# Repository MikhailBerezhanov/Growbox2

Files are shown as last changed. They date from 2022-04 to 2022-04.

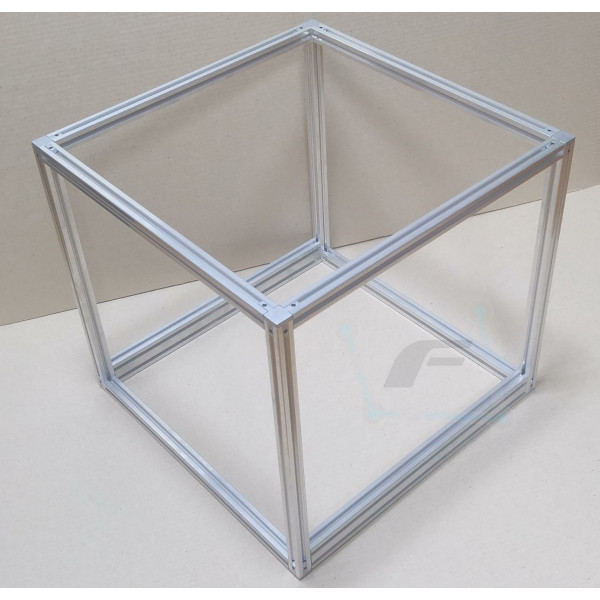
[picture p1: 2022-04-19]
case_design/3D_body/Чертежи/DY-4044-1-600x600.jpg

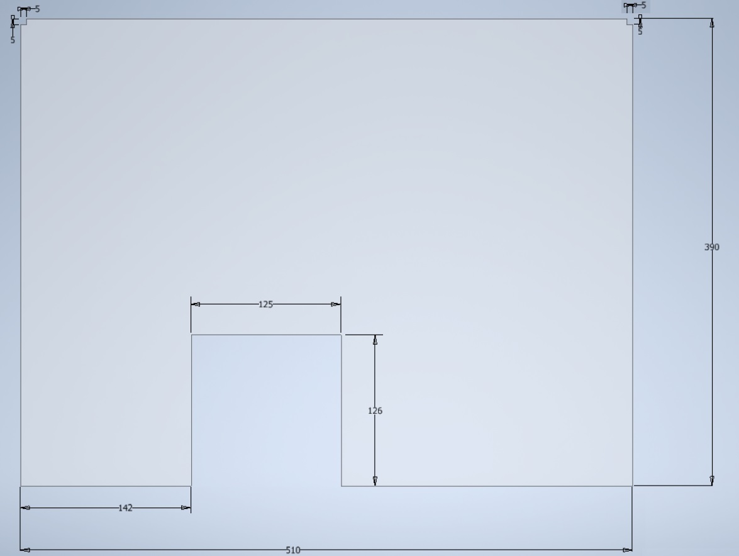
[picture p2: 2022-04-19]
case_design/3D_body/Чертежи/БокСтенка1.jpg

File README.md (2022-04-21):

# Growbox2
### Automated plants growing indoor system

([Learn more about this project](https://habr.com/ru/post/521414/))

3Dmodel

Growbox2 is an indoor system that takes care of your plants. It helps with:

* Watering
* Lighting
* Climate control

It supports WEB-UI to configure and check all function.



### How does it work

The system is based on 3 boards: 

* __Khadas VIM1__ - host MPU
* __FLC-01__ - self-made fitolamp controller
* __SensorsController__ - some kind of adapter from sensors-data to I2C bus 

Connection is the following:  



Host board runs __Ubuntu18.04 Linux__ and provides WEB-server that is available via Ethernet or WIFI connection.  
WEB interface is based on AJAX technology, so any sensor data is updated by request. You can use your __Browser__ to configure and watch the box system parameters. 

### IP address settings

There are different options in Growbox IP address configuration:

* __WIFI connection__ - by default system runs in WIFI Access Point (AP) mode, so using your smartphone you can
  1. find wifi-net called _Growbox_, 
  2. connect it, 
  3. see UI from mobile browser.  
That allows you to perform further configuration. 

*Technically WIFI mode could be configured to Client mode for wireless connection with your router, but this feature not implemented yet in _Settings_ menu.

* __LAN connection__ - by default system has dynamic IP (DHCP is on), so you'll need to
  1. check what address device got in your router menu,
  2. open this IP in Browser to get access to system UI   
Afterwards, LAN IP address can be changed to static in _Settings_ menu.

### Software

UI backend part is the CGI-application that runs on NGINX webserver.  

For _Debian \ Ubuntu_ backend dependencies installed as:  
`sudo apt install gcc g++ make nginx sqlite3 libconfig-dev libfcgi-dev libsqlite3-dev isc-dhcp-server hostapd`

Frontend part can be found in `UI/data` subfolder and has all dependencies inside to let system work without Internet connection.

Optionally application can be installed on target by calling `UI/install.sh` script. That will add __systemd__ service that can be controlled by _systemctl_ commands:

``` sh
# Run backend and check it's status
systemctl start gbweb
systemctl status gbweb
# Stop backend
systemctl stop gbweb
```

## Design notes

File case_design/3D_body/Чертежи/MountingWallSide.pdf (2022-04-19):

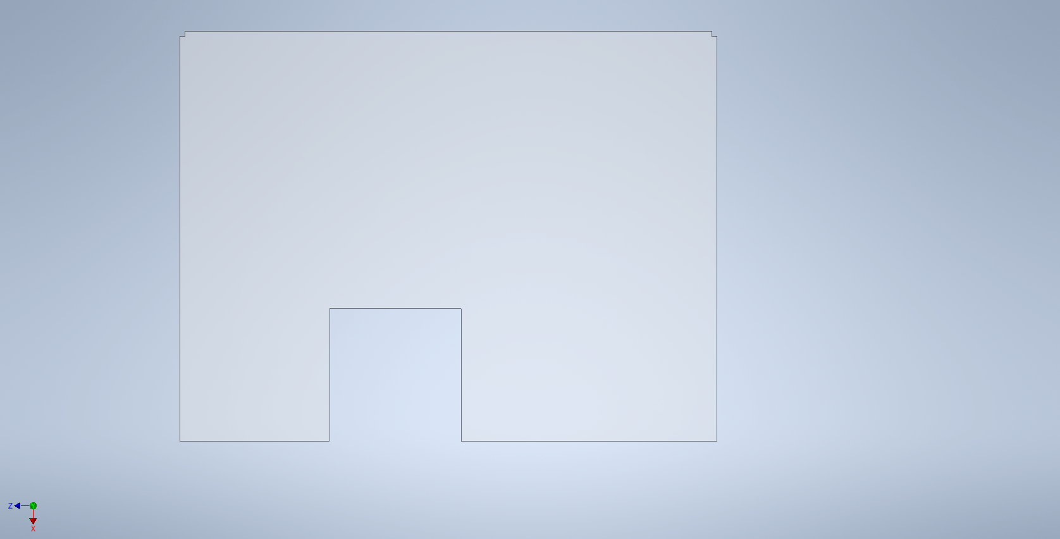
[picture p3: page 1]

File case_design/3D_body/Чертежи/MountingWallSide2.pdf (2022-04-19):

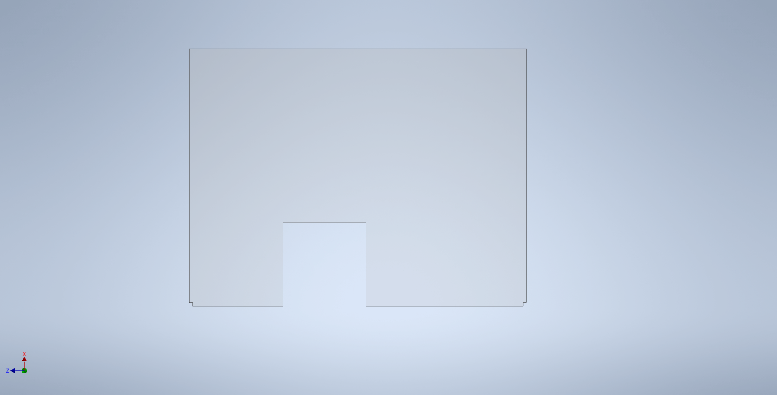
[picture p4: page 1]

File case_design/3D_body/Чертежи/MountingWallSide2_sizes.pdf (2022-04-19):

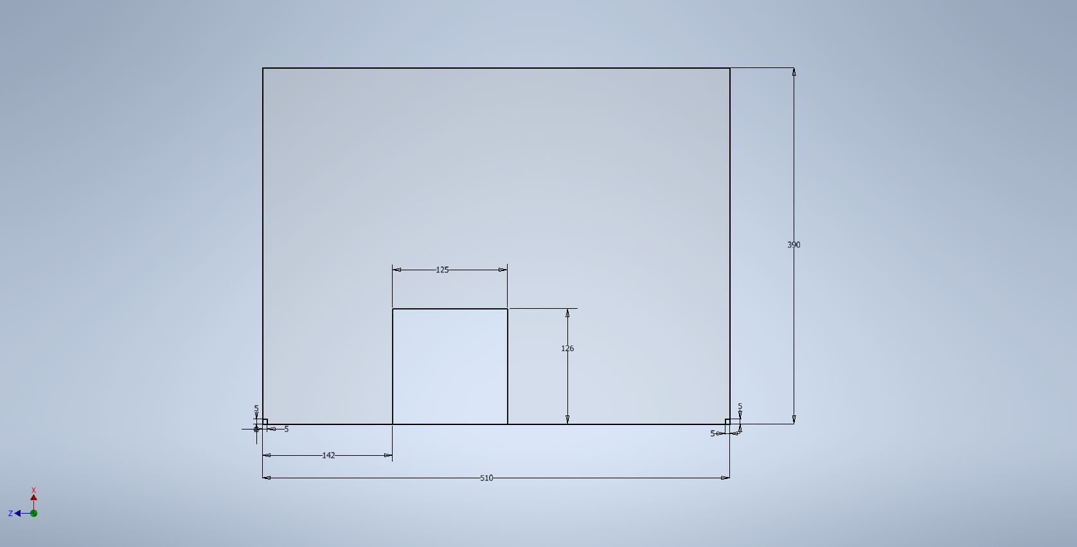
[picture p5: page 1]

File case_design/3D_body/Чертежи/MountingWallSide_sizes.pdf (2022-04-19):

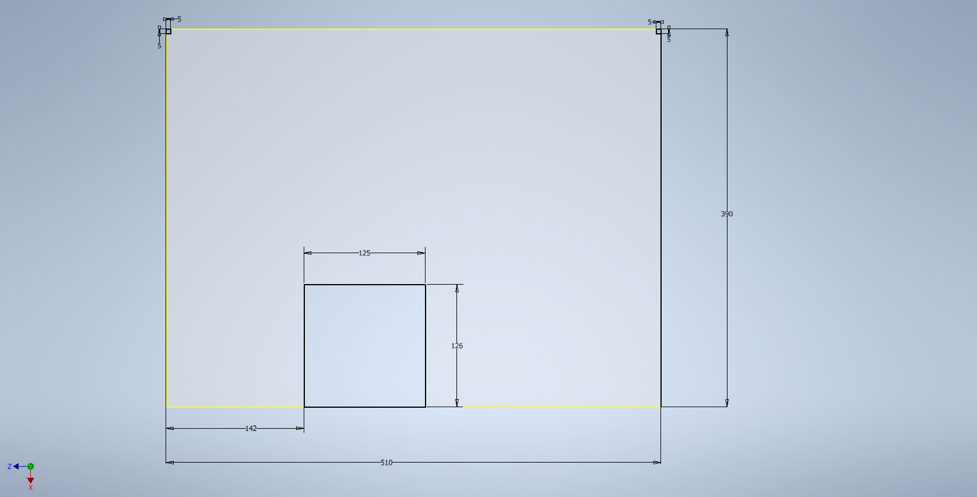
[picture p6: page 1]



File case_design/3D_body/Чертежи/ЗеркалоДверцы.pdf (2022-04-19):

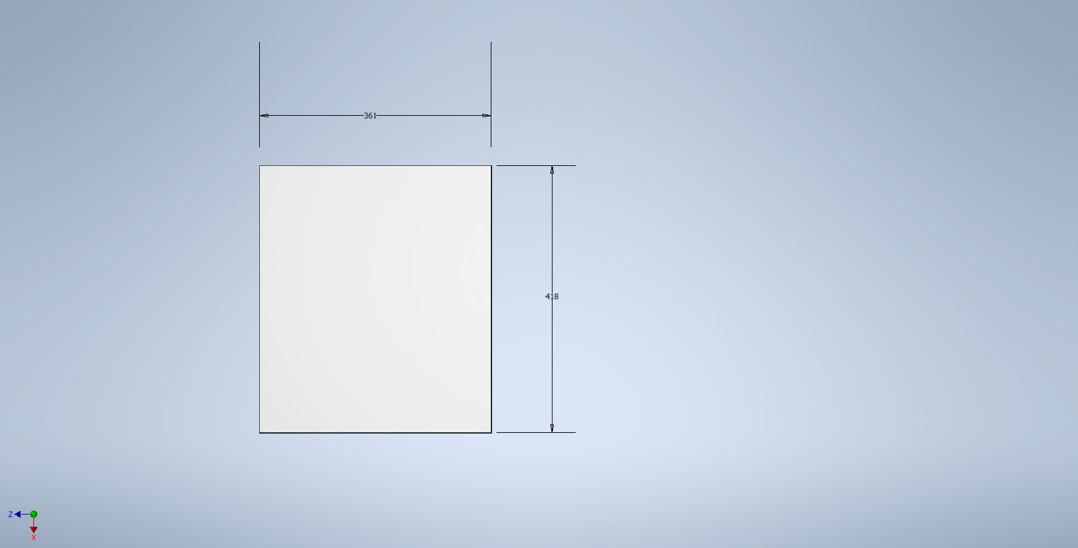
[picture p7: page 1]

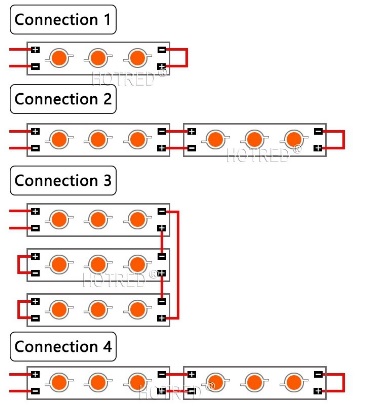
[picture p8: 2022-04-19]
case_design/led_strips_conn2.jpg

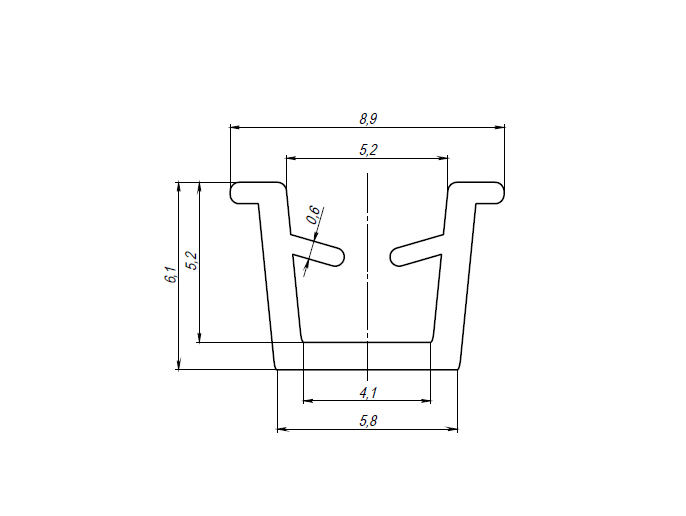
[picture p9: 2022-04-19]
case_design/Z19_chertezh.jpg

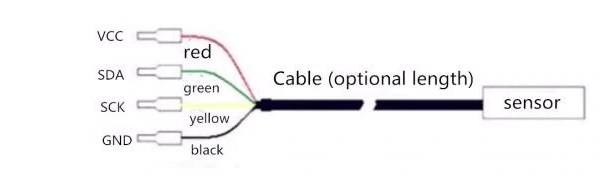
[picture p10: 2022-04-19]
boards/sensors/TempHumSensor/sensor_pinout.jpg

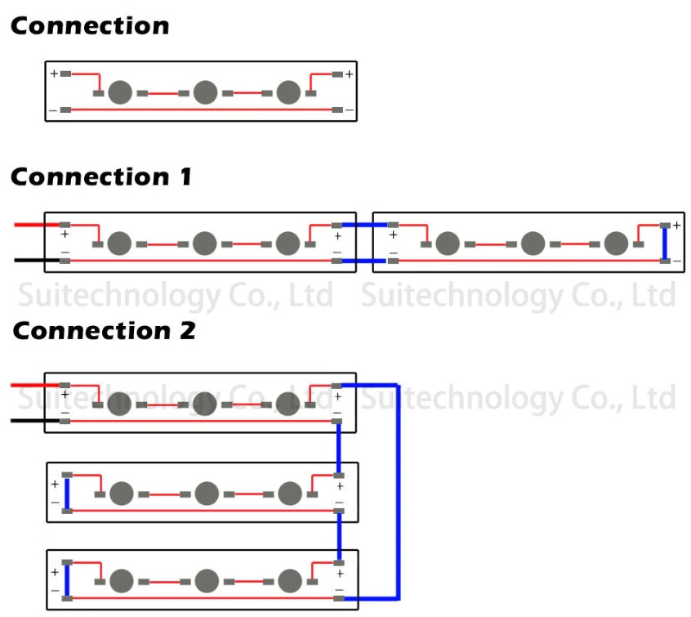
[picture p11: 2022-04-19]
case_design/led_strips_connection.jpg

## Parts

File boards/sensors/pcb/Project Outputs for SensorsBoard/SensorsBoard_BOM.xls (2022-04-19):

Comment | Description | Designator | Quantity
K50-35 63V 47uF | Конденсатор электролитический алюминиевый | C1 | 1
1210 1uF X7R 100V | Cap SMD1210 | C2 | 1
K50-35 35V 220uF | Конденсатор электролитический алюминиевый | C3 | 1
0805 1uF 25V X7R | SMD Cap 0805 | C4 | 1
K50-35 10V 100uF | Конденсатор электролитический алюминиевый | C5 | 1 | https://www.chipdip.ru/product0/311944248?from=suggest_product
LM2596HV - 12V | SIMPLE SWITCHER4; 4V to 60V, 3A Low Component Count Step-Down Regulator | DA1 | 1 | https://www.chipdip.ru/product/lm2596hvgr-12
КР142ЕН5А | Cтабилизатор напряжения положительной полярности с выходным напряжением 5 В | DA2 | 1 | https://www.chipdip.ru/product/kr142en5a
RDC1-0014 | Встраиваемый DC/DC преобразователь 60В 3А | DA3 | 1
STM32F103_BLUEPILL | STM32F103_BLUEPILL | DD1 | 1
RLB0914-470KL | Радиальные выводные индуктивности | L1 | 1
SRR1208-330YL | Fixed Inductors 6800uH 10% SMD 1208 | L2 | 1
0805 10k | SMD Res 0805 | R1, R2 | 2
7.5k 1% | Throu hole resistor | R3 | 1 | https://www.chipdip.ru/product0/43763
0805 0 | SMD Res 0805 | R4 | 1
BZX55C3V3 | Stabilitron 3.3V | VD1 | 1
SS36 | Rectifier, Schottky; DO-214AB; 3.0A IF; 0.75V; 60V; 100A IFRM; 10000V/us; 1000pF | VD2 | 1
SS26T3G | Диод Шоттки 2А 60В [SMB / DO-214AA] | VD3 | 1
DS1069-4M | Вилка на плату 2.50мм | X1 | 1
300-041-12 | Клеммник винтовой, 4-контактный, 5мм, прямой | X2 | 1
Conn_Molex_47053-1000_eec | CONN 4 Positions Header, Unshrouded Connector 0.100" (2.54mm) Through Hole Tin | X3 | 1
DS1021_1x4 | Вилка штыревая 2.54мм 1x4 прямая тип1 | X4, X5 | 2
Conn_Molex_47053-1000_eec | CONN 4 Positions Header, Unshrouded Connector 0.100" (2.54mm) Through Hole Tin | X6 | 1
DS1021_1x8 | Вилка штыревая 2.54мм 1x8 прямая тип1 | X7, X8 | 2
300-021-12 | Klemmnik 2 | X9 | 1

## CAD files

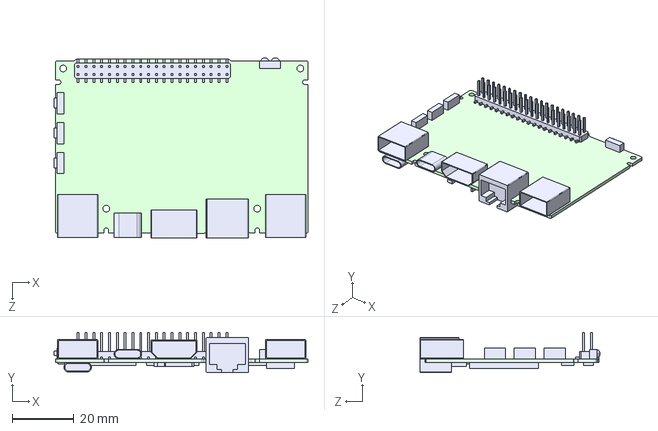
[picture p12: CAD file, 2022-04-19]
boards/host/Khadas VIM1/edge-v-11.STEP
82.5 x 13.1 x 58.6 mm

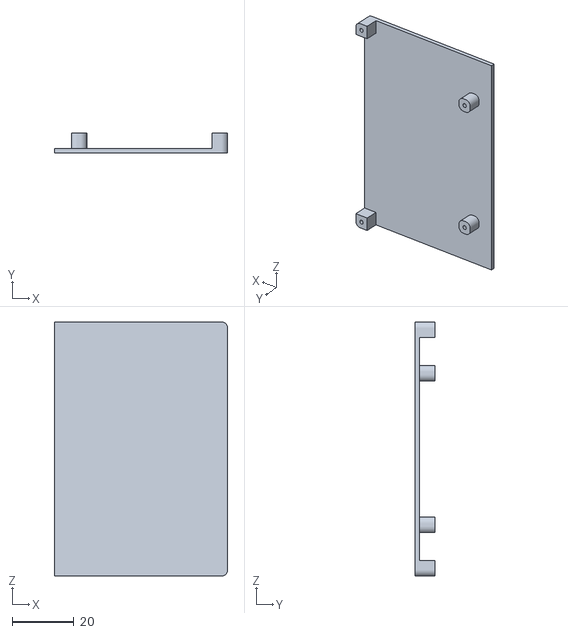
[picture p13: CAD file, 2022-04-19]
case_design/3D_body/ForPrint/VIM1_Holder.stl
56.0 x 6.50 x 82.0

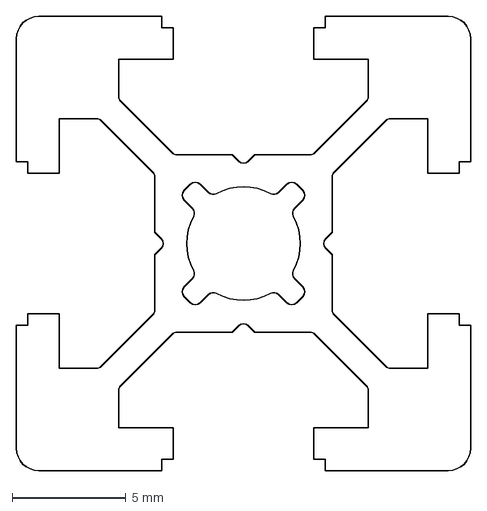
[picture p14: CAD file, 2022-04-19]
case_design/3D_body/Чертежи/OB-2020.DXF
20.0 x 20.0 mm

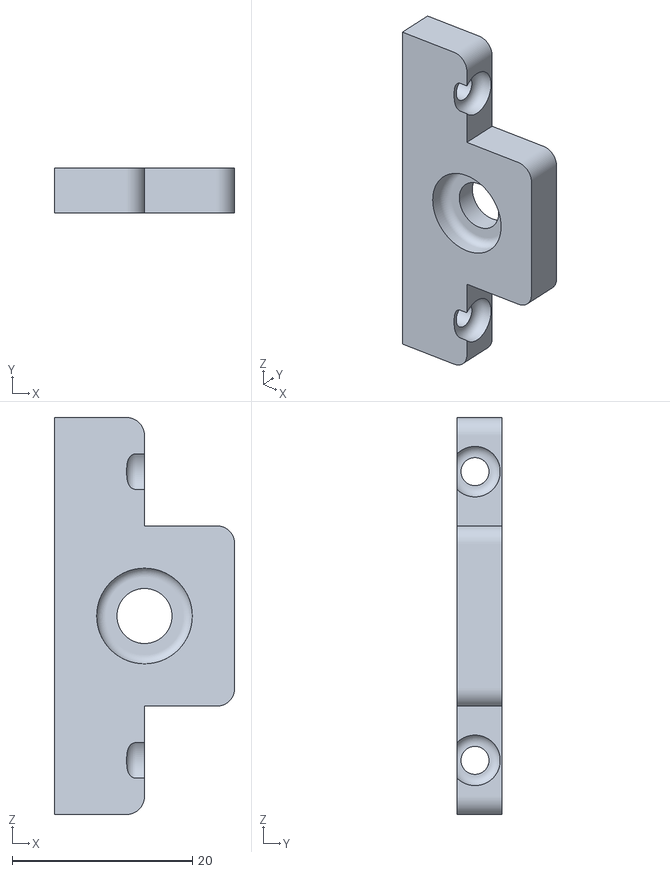
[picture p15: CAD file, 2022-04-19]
case_design/3D_body/ForPrint/RaditorFastener2.stl
20.0 x 5.00 x 44.0

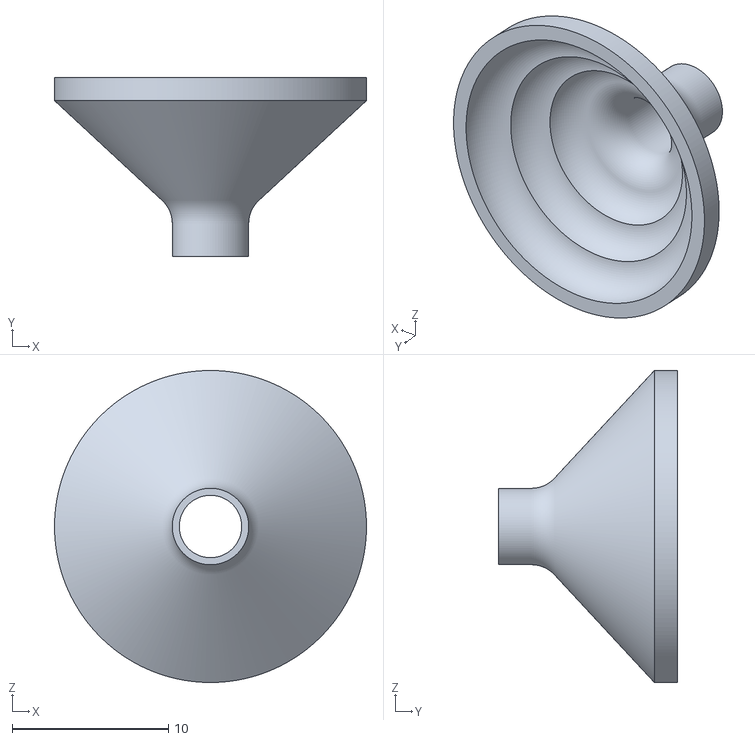
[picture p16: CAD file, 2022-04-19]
case_design/3D_body/ForPrint/TubeExpander.stl
20.0 x 11.5 x 20.0

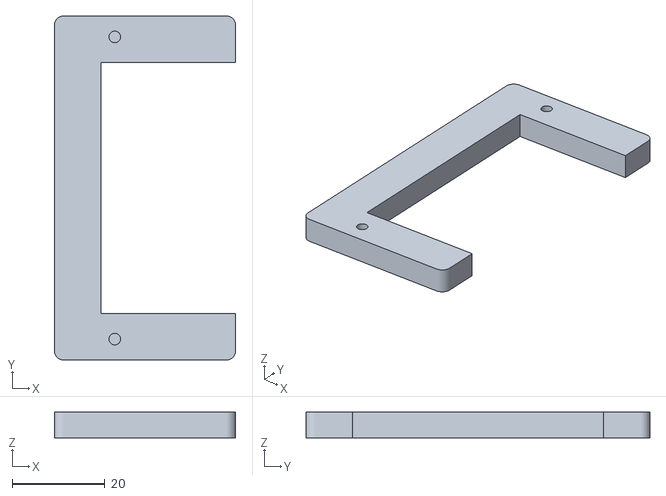
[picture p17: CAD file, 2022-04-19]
case_design/3D_body/ForPrint/S-10-5_Holder.stl
39.0 x 74.0 x 5.50

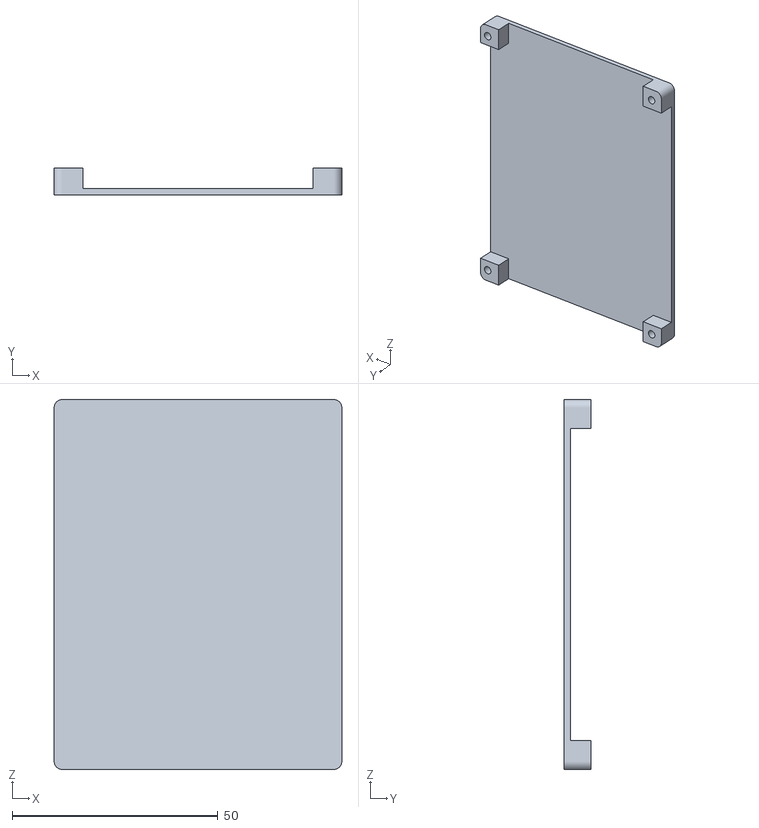
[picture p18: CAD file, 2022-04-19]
case_design/3D_body/ForPrint/SensorsC_Holder.stl
70.0 x 6.50 x 90.0

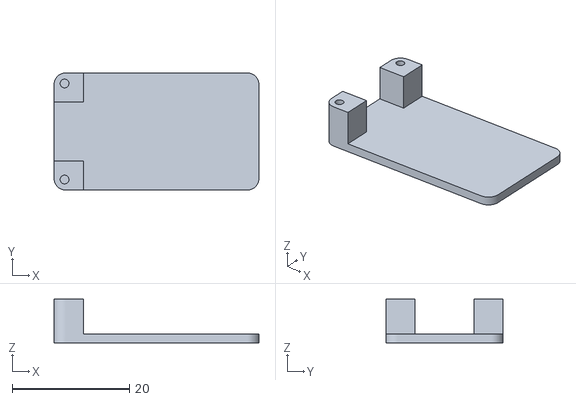
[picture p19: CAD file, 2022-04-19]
case_design/3D_body/ForPrint/RDC1-0014_Holder.stl
35.0 x 20.0 x 7.50

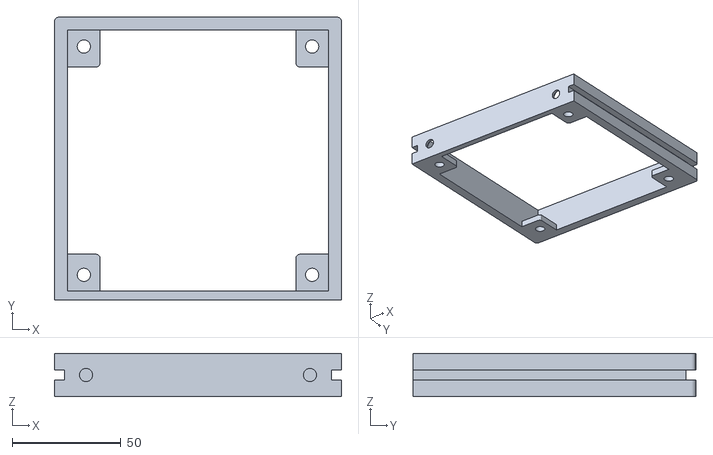
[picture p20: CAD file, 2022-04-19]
case_design/3D_body/ForPrint/CoolerFastener.stl
132.0 x 130.0 x 20.0

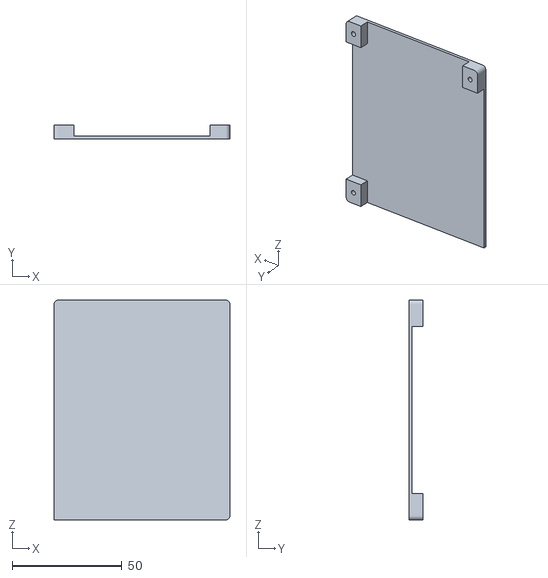
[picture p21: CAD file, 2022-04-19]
case_design/3D_body/ForPrint/FLC_Holder.stl
80.0 x 6.50 x 100.0

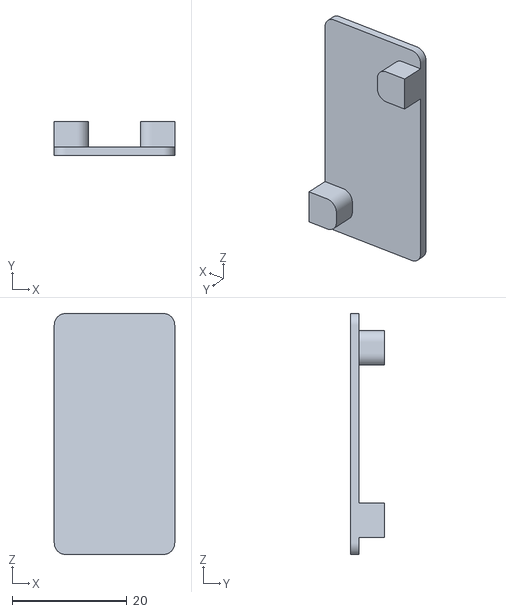
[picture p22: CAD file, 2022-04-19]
case_design/3D_body/ForPrint/DCDC_Holder.stl
21.0 x 6.00 x 42.0

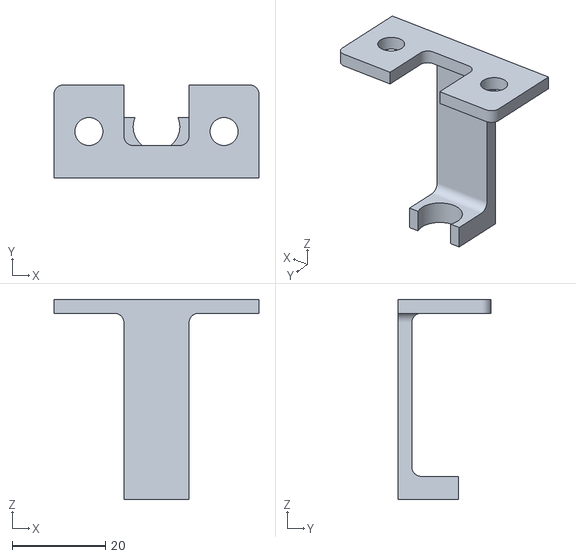
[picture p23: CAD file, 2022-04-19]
case_design/3D_body/ForPrint/TempSensorHolder.stl
44.0 x 20.0 x 43.0

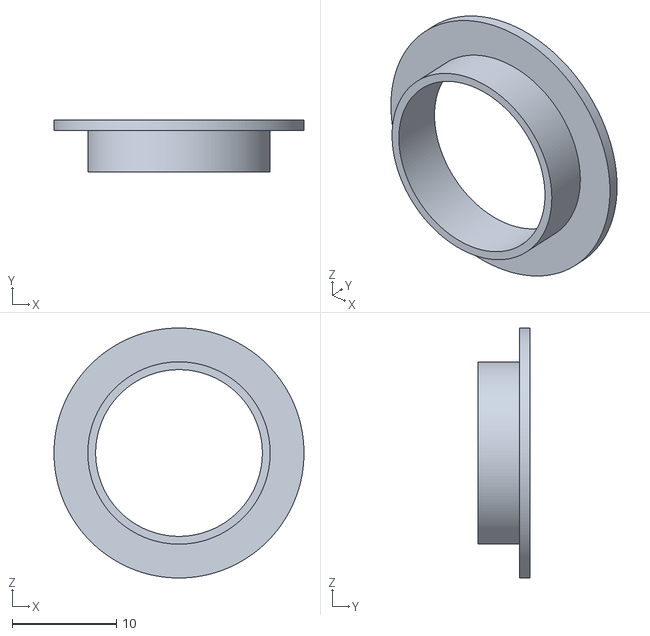
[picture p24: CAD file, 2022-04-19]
case_design/3D_body/ForPrint/Blumat_holder.stl
24.0 x 5.00 x 24.0

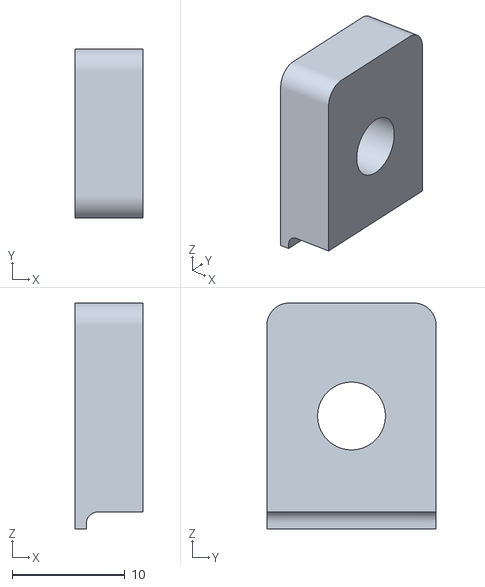
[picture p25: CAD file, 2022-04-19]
case_design/3D_body/ForPrint/CableHolder.stl
6.00 x 15.0 x 20.0

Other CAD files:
case_design/3D_body/ForPrint/TubeExpander2.stl
case_design/3D_body/2004.ipt
case_design/3D_body/Blumat_holder.ipt
case_design/3D_body/CableHolder.ipt
case_design/3D_body/DCDC_Holder.ipt
case_design/3D_body/FLC_3D/1437566-3.iam
case_design/3D_body/FLC_3D/1N4002.iam
case_design/3D_body/FLC_3D/3mm_LED.iam
case_design/3D_body/FLC_3D/3mm_LED_1.iam
case_design/3D_body/FLC_3D/3mm_LED_2.iam
case_design/3D_body/FLC_3D/5970839968.ipt
case_design/3D_body/FLC_3D/6276159808.iam
case_design/3D_body/FLC_3D/BAT54C,215.iam
case_design/3D_body/FLC_3D/Board.iam
case_design/3D_body/FLC_3D/Body.ipt
case_design/3D_body/FLC_3D/Body_1.ipt
case_design/3D_body/FLC_3D/Body_2.ipt
case_design/3D_body/FLC_3D/C1.iam
case_design/3D_body/FLC_3D/C10.iam
case_design/3D_body/FLC_3D/C11.iam
case_design/3D_body/FLC_3D/C12.iam
case_design/3D_body/FLC_3D/C13.iam
case_design/3D_body/FLC_3D/C14.iam
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

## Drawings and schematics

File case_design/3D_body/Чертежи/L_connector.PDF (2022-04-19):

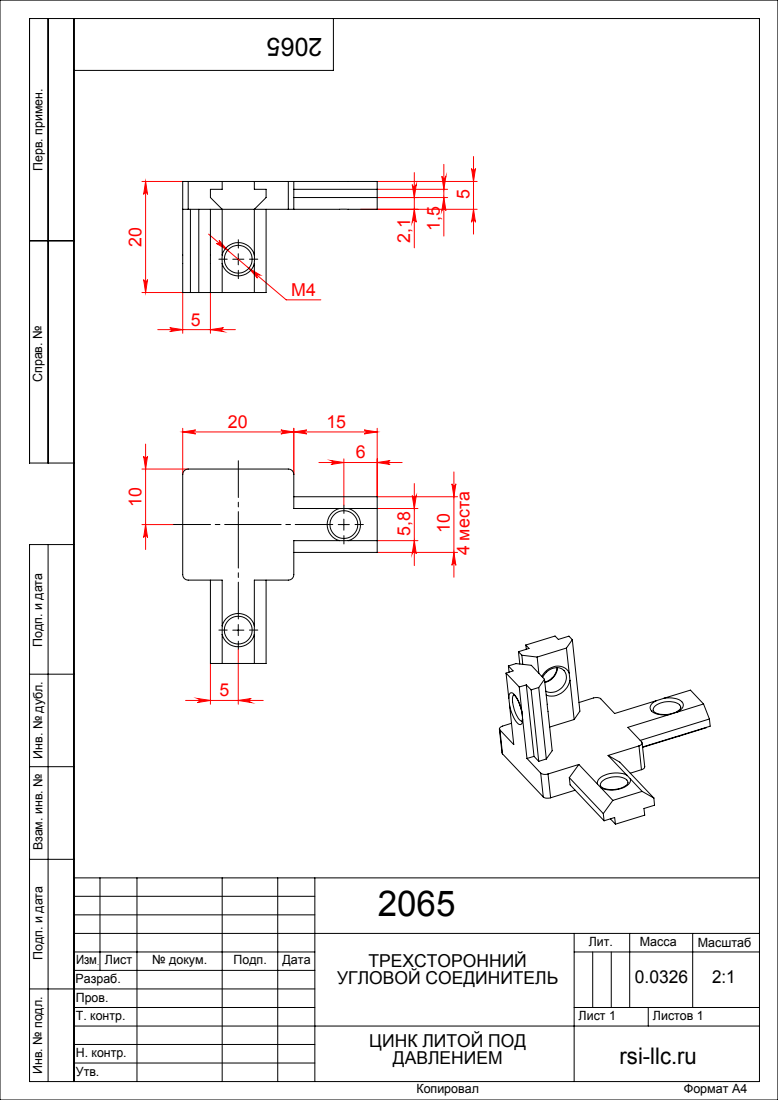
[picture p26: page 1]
4 места; Копировал; Формат А4

Справ. № Перв. примен. Подп. и дата Инв. № дубл. Взам. инв. № Подп. и дата Инв. № подл.

ТРЕХСТОРОННИЙ УГЛОВОЙ СОЕДИНИТЕЛЬ | Лит. | Масса | Масштаб

Изм. | Лист | № докум. | Подп. | Дата | | | | | 0.0326 | 2:1
Разраб.
Пров.
Т. контр. | | | | | Лист 1 | Листов 1

ЦИНК ЛИТОЙ ПОД ДАВЛЕНИЕМ | rsi-llc.ru

Н. контр.
Утв.

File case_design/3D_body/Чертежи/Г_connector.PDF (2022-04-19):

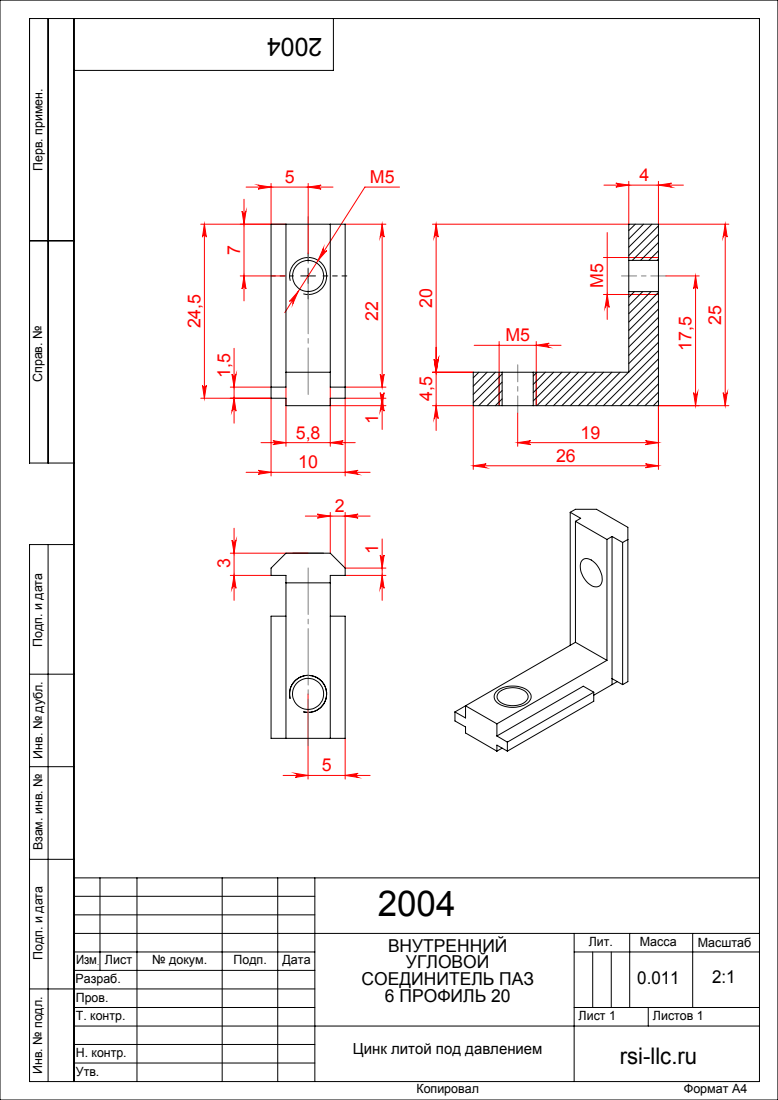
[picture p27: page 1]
Копировал; Формат А4

Справ. № Перв. примен. Подп. и дата Инв. № дубл. Взам. инв. № Подп. и дата Инв. № подл.

ВНУТРЕННИЙ УГЛОВОЙ СОЕДИНИТЕЛЬ ПАЗ 6 ПРОФИЛЬ 20 | Лит. | Масса | Масштаб

Изм. | Лист | № докум. | Подп. | Дата | | | | | 0.011 | 2:1
Разраб.
Пров.
Т. контр. | | | | | Лист 1 | Листов 1

Цинк литой под давлением | rsi-llc.ru

Н. контр.
Утв.

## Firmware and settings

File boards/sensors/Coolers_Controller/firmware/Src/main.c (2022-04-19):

#include <stdio.h>
#include <string.h>

#include "stm32f1xx_hal.h"
#include "uart.h"
#include "timer.h"
#include "i2c.h"
#include "flash.h"


#define DEBUG_MSG 1
#include "dbgmsg.h"


// I2C-slave registers map
#define COOLER1_REG		0x10		// set cooler1 pwm (0..100)
#define COOLER2_REG		0x20		// set cooler2 pwm (0..100)
#define STATUS1_REG		0x11		// get cooler1 current pwm value
#define STATUS2_REG		0x21		// get cooler2 current pwm value

/* Private variables ---------------------------------------------------------*/
IWDG_HandleTypeDef hiwdg;

uint8_t i2cBuf[2] = {0,0};
uint32_t coolers_pwm[2] = {0,0};


/* Private function prototypes -----------------------------------------------*/
static int SystemClock_Config(void);
static void GPIO_Init(void);
static void IWDG_Init(void);

int main(void)
{	
  /* Reset of all peripherals, Initializes the Flash interface and the Systick. */
  HAL_Init();
	GPIO_Init();
  /* Configure the system clock */
  int res = SystemClock_Config();

  /* Initialize all configured peripherals */
	UART1_Init(115200);		// debug port	
	if(res < 0) errmsg("SystemClock_Config() failed (%d)\r\n", res);
  
  TIM3_PWM_Init();
	I2C1_Init();
  IWDG_Init();
	flash_read_page(ADDR_FLASH_PAGE_127, coolers_pwm, sizeof(coolers_pwm));
	for (int i = 0; i < sizeof(coolers_pwm); i++){
		if (coolers_pwm[i] > 100) coolers_pwm[i] = 100;
	}
	
	dbgmsg("~ Cooler Controller starts ~\r\n");
	dbgmsg("Cooler1 PWM: %u, Cooler2 PWM: %u\r\n", coolers_pwm[0], coolers_pwm[1]);
	
	
	TIM3_PWM_ConfigAndStart(TIM_CHANNEL_1, 0);
	TIM3_PWM_ConfigAndStart(TIM_CHANNEL_3, 0);
	
	uint32_t cnt = 0;
	
	
  while (1)
  {
		HAL_I2C_EnableListen_IT(&hi2c1);
		cnt++;
		if(cnt >= 300000){
			HAL_GPIO_TogglePin(GPIOC, GPIO_PIN_13);
			cnt = 0;
		}
		
		if(I2C_transferRequested)
		{
			HAL_I2C_Slave_Seq_Receive_IT(&hi2c1, i2cBuf, 1, I2C_FIRST_FRAME);
			while (HAL_I2C_GetState(&hi2c1) != HAL_I2C_STATE_LISTEN);
			
			// Writing to register
			if((i2cBuf[0] == COOLER1_REG) || (i2cBuf[0] == COOLER2_REG)) 
			{
				HAL_I2C_Slave_Seq_Receive_IT(&hi2c1, &i2cBuf[1], 1, I2C_LAST_FRAME);
				while (HAL_I2C_GetState(&hi2c1) != HAL_I2C_STATE_LISTEN);
				
				dbgmsg("I2C: set 0x%02X to 0x%02X\r\n", i2cBuf[0], i2cBuf[1]);
				if(i2cBuf[1] > 100) i2cBuf[1] = 100;
				
				switch(i2cBuf[0])
				{
					case COOLER1_REG:
						TIM3_PWM_ConfigAndStart(TIM_CHANNEL_1, i2cBuf[1]);
						coolers_pwm[0] = i2cBuf[1];
						flash_write_page(ADDR_FLASH_PAGE_127, coolers_pwm, 2);
						break;
					
					case COOLER2_REG:
						TIM3_PWM_ConfigAndStart(TIM_CHANNEL_3, i2cBuf[1]);
						coolers_pwm[1] = i2cBuf[1];
						flash_write_page(ADDR_FLASH_PAGE_127, coolers_pwm, 2);
						break;
				}
			}
			// Reading register
			else
			{
				//HAL_Delay(1);		
				dbgmsg("I2C: get 0x%02X ", i2cBuf[0]);

				uint8_t responce = 0xFF; // Default value
				
				switch (i2cBuf[0])
				{
					case STATUS1_REG:
						responce = (uint8_t)coolers_pwm[0];
						break;
					
					case STATUS2_REG:
						responce = (uint8_t)coolers_pwm[1];
						break;
				}
				
				dbgmsg("sending 0x%02X\r\n", responce);
				
				HAL_I2C_Slave_Seq_Transmit_IT(&hi2c1, &responce, 1, I2C_LAST_FRAME);
				while (HAL_I2C_GetState(&hi2c1) != HAL_I2C_STATE_READY);
			}
			
			I2C_transferRequested = 0;
			I2C_transferDir = I2C_DIR_UNKNOWN;
			HAL_I2C_EnableListen_IT(&hi2c1);
		}

		HAL_IWDG_Refresh(&hiwdg);
  }

}

void HAL_MspInit(void)
{
  __HAL_RCC_AFIO_CLK_ENABLE();
  __HAL_RCC_PWR_CLK_ENABLE();

  /* System interrupt init*/

  /** NOJTAG: JTAG-DP Disabled and SW-DP Enabled */
  __HAL_AFIO_REMAP_SWJ_NOJTAG();
}

/**
  * @brief System Clock Configuration
  * @retval None
  */
static int SystemClock_Config(void)
{
  RCC_OscInitTypeDef RCC_OscInitStruct = {0};
  RCC_ClkInitTypeDef RCC_ClkInitStruct = {0};
  RCC_PeriphCLKInitTypeDef PeriphClkInit = {0};

  /** Initializes the CPU, AHB and APB busses clocks */
  RCC_OscInitStruct.OscillatorType = RCC_OSCILLATORTYPE_LSI|RCC_OSCILLATORTYPE_HSE
                              |RCC_OSCILLATORTYPE_LSE;
  RCC_OscInitStruct.HSEState = RCC_HSE_ON;
  RCC_OscInitStruct.HSEPredivValue = RCC_HSE_PREDIV_DIV1;
  RCC_OscInitStruct.LSEState = RCC_LSE_ON;
  RCC_OscInitStruct.HSIState = RCC_HSI_ON;
  RCC_OscInitStruct.LSIState = RCC_LSI_ON;
  RCC_OscInitStruct.PLL.PLLState = RCC_PLL_ON;
  RCC_OscInitStruct.PLL.PLLSource = RCC_PLLSOURCE_HSE;
  RCC_OscInitStruct.PLL.PLLMUL = RCC_PLL_MUL9;
  if (HAL_RCC_OscConfig(&RCC_OscInitStruct) != HAL_OK) 
		return -1;

  /** Initializes the CPU, AHB and APB busses clocks */
  RCC_ClkInitStruct.ClockType = RCC_CLOCKTYPE_HCLK|RCC_CLOCKTYPE_SYSCLK
                              |RCC_CLOCKTYPE_PCLK1|RCC_CLOCKTYPE_PCLK2;
  RCC_ClkInitStruct.SYSCLKSource = RCC_SYSCLKSOURCE_PLLCLK;
  RCC_ClkInitStruct.AHBCLKDivider = RCC_SYSCLK_DIV1;
  RCC_ClkInitStruct.APB1CLKDivider = RCC_HCLK_DIV2;
  RCC_ClkInitStruct.APB2CLKDivider = RCC_HCLK_DIV1;

  if (HAL_RCC_ClockConfig(&RCC_ClkInitStruct, FLASH_LATENCY_2) != HAL_OK)
		return -2;
	
  PeriphClkInit.PeriphClockSelection = RCC_PERIPHCLK_RTC;
  PeriphClkInit.RTCClockSelection = RCC_RTCCLKSOURCE_LSE;
  if (HAL_RCCEx_PeriphCLKConfig(&PeriphClkInit) != HAL_OK)
		return -3;
	
	return 0;
}

/**
  * @brief IWDG Initialization Function
  * @param None
  * @retval None
  */
static void IWDG_Init(void)
{
  hiwdg.Instance = IWDG;
  hiwdg.Init.Prescaler = IWDG_PRESCALER_16;
  hiwdg.Init.Reload = 4095;
  if (HAL_IWDG_Init(&hiwdg) != HAL_OK)
  {
    errmsg("HAL_IWDG_Init() failed\r\n");
  }
}

/**
  * @brief GPIO Initialization Function
  * @param None
  * @retval None
  */
static void GPIO_Init(void)
{
  GPIO_InitTypeDef GPIO_InitStruct = {0};

  /* GPIO Ports Clock Enable */
  __HAL_RCC_GPIOC_CLK_ENABLE();

  /*Configure GPIO pin : PC13 */
  GPIO_InitStruct.Pin = GPIO_PIN_13;
  GPIO_InitStruct.Mode = GPIO_MODE_OUTPUT_PP;
  GPIO_InitStruct.Pull = GPIO_NOPULL;
  GPIO_InitStruct.Speed = GPIO_SPEED_FREQ_LOW;
  HAL_GPIO_Init(GPIOC, &GPIO_InitStruct);  
	
	/*Configure GPIO pin Output Level */
  HAL_GPIO_WritePin(GPIOC, GPIO_PIN_13, GPIO_PIN_RESET);

}

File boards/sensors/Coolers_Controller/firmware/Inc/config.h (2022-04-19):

#ifndef	_CONFIG_H
#define	_CONFIG_H

// NVIC Priorities  0 – MAX, 15 – MIN
// We use PriorityGroup_4 in HAL_Init, so 0..15 Preemption priorities
/*
 ===============================================================================
    NVIC_PriorityGroup 	|  
  ============================================================================== 
   NVIC_PriorityGroup_0 | 0 		| 0 bits for pre-emption priority
                        | 0-15	|	4 bits for subpriority
  -------------------------------------------------- --------------------------- 
   NVIC_PriorityGroup_1 | 0-1 	| 1 bits for pre-emption priority
                        |	0-7 	|	3 bits for subpriority
  -------------------------------------------------- ---------------------------     
   NVIC_PriorityGroup_2 | 0-3 	| 2 bits for pre-emption priority
                        |	0-3  	| 2 bits for subpriority
  -------------------------------------------------- ---------------------------     
   NVIC_PriorityGroup_3 | 0-7   | 3 bits for pre-emption priority
                        |	0-1 	| 1 bits for subpriority
  -------------------------------------------------- ---------------------------    
   NVIC_PriorityGroup_4 | 0-15  | 4 bits for pre-emption priority
                        |	0  		|	0 bits for subpriority                       
  ==============================================================================
*/
#define BL_KEY_Pin 					GPIO_PIN_3
#define BL_KEY_GPIO_Port 		GPIOA
#define BL_CONN_Pin 				GPIO_PIN_4
#define BL_CONN_GPIO_Port 	GPIOA
#define BL_nRST_Pin 				GPIO_PIN_1
#define BL_nRST_GPIO_Port 	GPIOB

#define USART1_PreP		5

#define USART3_PreP		6

#define TIM2_PreP			13			// General purpose timer

#define TIM4_PreP			7				// RTC poll timer

#define RTC_PreP			7

#define I2C1_EV_PreP	0				// I2C event
#define I2C1_ER_PreP	0				// I2C error

#endif	//_CONFIG_H
